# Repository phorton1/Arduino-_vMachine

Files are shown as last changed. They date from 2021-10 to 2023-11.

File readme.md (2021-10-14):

# The vMachine - Home

**Home** --
**[History](docs/history.md)** --
**[Hardware](docs/hardware.md)** --
**[Electronics](docs/electronics.md)** --
**[User Interface](docs/ui.md)** --
**[Software](docs/software.md)** --
**[Installation](docs/installation.md)**

The vMachine is a full featured proof-of-concept implementation of a **V plotter**.
It is essentially a CNC machine that uses *triangular kinematics* to work in a
cartesian coordinate system.

It is based on the inexpensive, yet powerful **ESP32** module, rather than the usual
Arduino class proessors.  The ESP32 can easily be programmed from within the
Arduino development environment and has *dual cores*, runs at *240 Mhz* (as opposed to
the Arduino at 16Mhz) and comes with *520KB* (as opposed to 2KB) *of RAM*.  In addition
the ESP32 includes full onboard **WiFi and Bluetooth** capabilities, and can be had for
$5, or about half the price of a genuine Arduino.

Therefore my *primary design decision* was to base this, and my future CNC projects
on an ESP32 processor.

**VIDEO - introduction to the vMachine**

The vMachine project is intended to accomplish several goals. Firstly, I wanted
to start developing and publishing open source CNC machines with the ESP32.
And so I built the machine and now present the designs and information
needed to build one.

The vMachine includes a full **Web Browser User Interface** so that it can be
controlled wirelessly from your phone or computer via **WiFi**.  It can also be controlled
via the **serial port** on the ESP32, via **Telnet** on port 23, or via **Bluetooth**
for usage with commonly available gcode sender programs.
Finally, it can also store gcode files on the optional **SD Card** and run jobs entirely
locally, right on the ESP32, via the optional **Touch Screen User Interface**, without
involving any other devices.

This repository includes all of the files and information needed to
build a copy of this machine.  It includes the needed to **3D print** the plastic
parts, as well as the underlying Fusion 360 designs if you need
or want to modify the 3D printed parts. It includes all of the **schematics**
and information needed to breadboard or otherwise create the electronic circuits,
as well as the KiCad files behind those, and the Flatcam and GCode files I used to
mill my own **circuit boards** for this version.

I have tried to provide a general roadmap for building a vMachine on these
pages.

A specific goal of this vMachine project is that it is generally scalable
to a larger machine, specifically one that can work with 4x8 feet sheets
of plywood, using a router to cut the plywood, as with the
[Maslow CNC](https://www.maslowcnc.com/).
Credits go to the Maslow team, as my vMachine source code actually
contains a port of the **Maslow triangular kinematics** to the ESP32.
I hope to build such a machine in the near future, and it should be
relatively straight-forward to scale this project up to a larger
machine of some sort.  The size of the machine is entirely parameterized
within the software and user interface.

But most importantly, this project establishes a **general approach** to
building ESP32 based CNC machines of various types, not only the vMachine
but also typical 3 and 4 axis CNC machines.  It is entirely based on the
next generation
[FluidNC](https://github.com/bdring/FluidNC)
project, a hugely important codebase that I have
forked and modified slightly so-as to better be able build projects
within the Arduino IDE development environment.

## Running the demo files

Included in this repository are a number of ready-to-go **gcode files**
that you can run on the vMachine.  It is beyond the scope of this project
to teach you how to use Inkscape, or Flatcam, or Fusion 360, or any other
available program to create gcode files to feed to the vMachine.

But, if you build the machine, and populate the SD card from this
repository, there are some gcode files you can use right away to
test it, verify it is working correctly, and even produce some nice
drawings.  You can view the contents of these gcode files to see what
kind of gcode the vMachine expects so that you can produce it with
any of the above programs, or by hand, as necessary.

**VIDEO - Running the Demo Files**

The video above demonstrates the touch screen UI, the browser
based Web/Wifi UI, and the serial terminal user interface by running the following
"programs" (gcode files) via one of the user interfaces:

- **homing** - first we "home" the machine
- **center.g** - moves the sled to the center of the page
- **ruler.g** - starts at the center and prints a simple ruler pattern
- **draw_boxes.g** - draws boxes on the board itself around the work area and 12x9" and 11x8.5" paper sizes
- **/test8.5x11/test8.5x11.ngc** - a sophisticated test that draws rulers, shapes, a compass and a sailboat
on 11x8.5" paper

When you get your vMachine working, the first thing you will print will probably be
the **ruler.g**, and you can do that by just manually moving the sled to the approximate
center of the work area, before you get **homing** working.   Once you can **home**
the machine, and you setup the G55 and G56 coordinate systems, you can run the
**draw_boxes.g** gcode to draw the work area, and 12x9 and 11x8.5 alignment boxes
directly on the board.  Then you can tape a piece of (US letter) paper in the
11x8.5 alignment box and print the **test8.5x11.ngc** reference test sheet on that.

## Documentation

The documentation starts with this page, and includes the following additional
pages:

- **[History](docs/history.md)** - my personal historical perspectives and
photos of early prototypes and previous versions of the vMachine.
- **[Hardware](docs/hardware.md)** - details the physical
construction of the vMachine, including the 3D printing and mechanical parts.
- **[Electronics](docs/electronics.md)** - the schematics and home made circuit
boards for the machine.
- **[User Interface](docs/ui.md)** - a synopsis of the behavior of the
vMachine and it's generalized **FluidNC_UI** user interface.
- **[Software](docs/software.md)** - an overview of the software architecture
of the vMachine and FluidNC.
- **[Installation](docs/Installation.md)** - instructions on building and installing
the vMachine firmware onto the ESP32 using the Arduino IDE environment.

It is recommended that you read all these pages BEFORE constructing a vMachine.
In my opinion if you are going to build a machine from these sources, or part of them,
you should **START** with the **[Installation](docs/Installation.md)**
page and the first thing you should do is *build the firmware and install it*
to a bare ESP32 dev module with just a USB cable.

As part of *that* process it is required that you verify and and utilize the browser
based WiFi UI to the module and upload some files to the file system on the ESP32,
so with just the bare ESP32 module you can verify that the firmware is installed,
test the Web UI, and make sure that it runs more or less correctly BEFORE investing
any time in 3D printing or creating breadboards or printed circuit boards.

In any case, all of these pages, and this source, is provided in the hopes that
you will find it useful and/or interesting.

## License

I'm gonna have to do something here.  Yech, I hate those headers in source files.

## Credits

- To the [Maslow CNC](https://www.maslowcnc.com/) team for the kinematics.

- To **bdring** and the [FluidNC Team](https://github.com/bdring/FluidNC) for the core of this project.

<br>
<hr>
<div style="text-align: right">
<a href='docs/history.md'>NEXT</a><i> - more about the vMachine ...</i>
</div>

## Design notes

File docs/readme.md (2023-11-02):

# The vMachine - Home

**Home** --
**[History](history.md)** --
**[Hardware](hardware.md)** --
**[Electronics](electronics.md)** --
**[Software](software.md)** --
**[Installation](installation.md)**

The vMachine is a full featured proof-of-concept implementation of a **V plotter**.
It is essentially a CNC machine that uses *triangular kinematics* to work in a
cartesian coordinate system.

It is based on the inexpensive, yet powerful **ESP32** module, rather than the usual
Arduino class processors.  The ESP32 can easily be programmed from within the
Arduino development environment and has *dual cores*, runs at *240 Mhz* (as opposed to
the Arduino at 16Mhz) and comes with *520KB* (as opposed to 2KB) *of RAM*.  In addition
the ESP32 includes full onboard **WiFi and Bluetooth** capabilities, and can be had for
$5, or about half the price of a genuine Arduino.

Therefore my *primary design decision* was to base this, and my future CNC projects,
on an ESP32 processor.

**TODO: VIDEO - introduction to the vMachine (good thumbnail for front image**

The vMachine project is intended to accomplish several goals. First, I wanted
to start developing and publishing open source CNC machines with the ESP32.
And so I built the machine and now present the designs and information
needed to build one.

The vMachine includes a full **Web Browser User Interface** so that it can be
controlled wirelessly from your phone or computer via **WiFi**.  It can also be controlled
via the **serial port** on the ESP32, via **Telnet** on port 23, or via **Bluetooth**
for usage with commonly available gcode sender programs.
Finally, it can also store gcode files on the optional **SD Card** and run jobs entirely
locally, right on the ESP32, via the optional
[**Touch Screen User Interface**](https://github.com/phorton1/Arduino-libraries-FluidNC_UI)
, without involving any other devices.

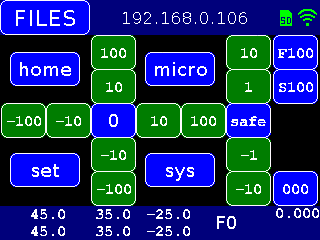
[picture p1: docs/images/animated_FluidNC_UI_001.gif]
(https://github.com/phorton1/Arduino-libraries-FluidNC_UI)


TODO: create animated gif specific to _vMachine

This repository includes all of the files and information needed to
build a copy of this machine.  It includes the files needed to **3D print** the plastic
parts, as well as the underlying Fusion 360 designs if you need
or want to modify the 3D printed parts. It includes all of the **schematics**
and information needed to breadboard or otherwise create the electronic circuits,
as well as the KiCad files behind those, and the Flatcam and GCode files I used to
mill my own **circuit boards** for this version.

I have tried to provide a general roadmap for building a vMachine on these
pages.

A specific goal of this vMachine project is that it is generally scalable
to a larger machine, specifically one that can work with 4x8 feet sheets
of plywood, using a router to cut the plywood, as with the
[Maslow CNC](https://www.maslowcnc.com/).
Credits go to the Maslow team, as this vMachine source code actually
contains a *port* of the **Maslow triangular kinematics** to the ESP32.
I hope to build such a machine in the near future, and it should be
relatively straight-forward to scale this project up to a larger
machine of some sort.  The size of the machine is entirely parameterized
within the software and user interface.

But most importantly, this project establishes a **general approach** to
building ESP32 based CNC machines of various types, not only the vMachine
but also typical 3 and 4 axis CNC machines or any other kind of machine
I might choose to build in the future.  It is entirely based on the
next generation
[FluidNC](https://github.com/bdring/FluidNC)
project, a hugely important codebase that I have
forked and modified slightly so-as to better be able build projects
within the Arduino IDE development environment.

<br>

## Running the demo files

Included in this repository are a number of ready-to-go **gcode files**
that you can run on the vMachine.  It is beyond the scope of this project
to teach you how to use Inkscape, or Flatcam, or Fusion 360, or any other
available program to create gcode files to feed to the vMachine. You
may use any of those, or any other program you wish, to create gcode
files for the vMachine.

But, if you build the machine, and populate the SD card from the **sdCard folder**
in this repository, there are some gcode files you can use right away to
test it, verify it is working correctly, and even produce some nice
drawings.  You can also view the contents of these gcode files to see what
kind of gcode the vMachine expects so that you can produce it with
any of the above programs, or by hand, as necessary.

**TODO: VIDEO - Running the vMachine Demo Files**

The video above demonstrates the touch screen UI, the browser
based Web/Wifi UI, and the serial terminal user interface by running the following
"programs" (gcode files) via one of the user interfaces:

- **homing** - first we "home" the machine
- **center.g** - moves the sled to the center of the page
- **ruler.g** - starts at the center and prints a simple ruler pattern
- **draw_boxes.g** - draws boxes on the board itself around the work area and 12x9" and 11x8.5" paper sizes
- **/test8.5x11/test8.5x11.ngc** - a sophisticated test that draws rulers, shapes, a compass and a sailboat
on 11x8.5" paper

When you build a vMachine, the first thing you will print will probably be
**ruler.g**, and you can do that by just manually moving the sled to the approximate
center of the work area, before you get **homing** working.   Once you can **home**
the machine, and you setup the G55 and G56 coordinate systems, you can run the
**draw_boxes.g** gcode to draw the work area, and 12x9 and 11x8.5 alignment boxes
directly on the board.  Then you can tape a piece of (US letter) paper in the
11x8.5 alignment box and print the full **test8.5x11.ngc** reference gcode on that.

TODO: Image of test gcode output

<br>

## Documentation

The documentation starts with this page, and includes the following additional
pages:

- **[History](history.md)** - my personal historical perspectives and
photos of early prototypes and previous versions of the vMachine.
- **[Hardware](hardware.md)** - details the physical
construction of the vMachine, including the 3D printing and mechanical parts.
- **[Electronics](electronics.md)** - the schematics and home made circuit
boards for the machine.
- **[Software](software.md)** - contains an overview of the
**software architecture** and details about how to **configure** the vMachine
- **[Installation](Installation.md)** - instructions on building and installing
the vMachine firmware onto the ESP32 using the Arduino IDE environment.

It is recommended that you read all these pages BEFORE constructing a vMachine.
If you are going to build a machine from these sources, or part of them,
you should **START** with the **[Installation](Installation.md)**
page and the first thing you should do is *build the firmware and install it*
to a bare ESP32 dev module with just a USB cable.

As part of *that* process it is required that you verify and utilize the browser
based WiFi UI to the module and upload some files to the file system on the ESP32,
so with just the bare ESP32 module you can verify that the firmware is installed,
test the Web UI, and make sure that it runs more or less correctly BEFORE investing
any time in 3D printing or creating breadboards or printed circuit boards.

In any case, all of these pages, and this source, is provided in the hopes that
you will find it useful and/or interesting.

<br>

## Please Also See

Please also see another CNC machine based on the same architecture,
my implementation of an ESP32 3 axis machine on an inexpensive
[**CNC 3018**](https://github.com/phorton1/Arduino-esp32_cnc3018)
from China [ebay](https://www.ebay.com/itm/392298131168).

These "machines"  are relatively small INO programs.  They are built on top of a
number of other libraries that provide the bulk of the functionality.

- [**FluidNC**](https://github.com/phorton1/Arduino-libraries-FluidNC) - the next generation **ESP32 GRBL** machine
- [**FluidNC_UI**](https://github.com/phorton1/Arduino-libraries-FluidNC_UI) - a *touch screen user interface* for FluidNC
- [**FluidNC_Extensions**](https://github.com/phorton1/Arduino-libraries-FluidNC_Extensions) - some extensions to FluidNC

The core of the machines, the GRBL (g-code) interpreter, is based on the
[**FluidNC**](https://github.com/phorton1/Arduino-libraries-FluidNC)
library.  The operational details of the machine, what g-codes
are supported, the basic serial command protocol, the wifi and webserver,
the machine configuration, and most functional aspects of the machine are
provided by this library.

On top of FluidNC I have built
[**FluidNC_UI**](https://github.com/phorton1/Arduino-libraries-FluidNC_UI),
the *touch screen user interface*, as a library that can optionally
used in ESP32 CNC projects.
Please see this library for a **description of the *User Interface***.

I have also added a
[**FluidNC_Extensions**](https://github.com/phorton1/Arduino-libraries-FluidNC_Extensions)
library that contains a number
of features that are used in this, and other machines based on this system.
This library contains methods and objects to abstract and extend the FluidNC
core.  Specific contents at this time include:

- some easy to use debug/info/error **output methods**
- methods to abstract the **state** of the FluidNC machine
- methods to abstract **control** of the FluidNC machine
- methods to supplement the FluidNC **configuration** system, and
- an implementation of **mesh bed levelling**

<br>

## Credits and License

This library is licensed under the
[GNU General Public License v3.0](https://github.com/phorton1/Arduino-_vMachine/tree/master/LICENSE.TXT)

**Credits**

- To the [Maslow CNC](https://www.maslowcnc.com/) team for the kinematics.
- To **bdring** and the **FluidNC Team**

<br>
<hr>
<div style="text-align: right">
<a href='history.md'>NEXT</a><i> - more about the vMachine ...</i>
</div>

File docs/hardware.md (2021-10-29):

# The vMachine - Hardware

**[Home](readme.md)** --
**[History](history.md)** --
**Hardware** --
**[Electronics](electronics.md)** --
**[Software](software.md)** --
**[Installation](installation.md)**

## Parts List

The following parts are needed and/or optional to construct the vMachine.

- the **board**
- two **NEMA 17 stepper motors**
- two one meter 4 wire **cables** with connectors for the stepper motors
- two 16 tooth 5mm GT2 **pullies** for the stepper motors
- two meters of 5mm GT2 **belt**
- one MG90 **RC Servo**
- one meter 3 wire **cable** with connectors for the servo
- two **infrared sensor boards** (from the [Electronics](electronics.md) page)
- two one meter 3 wire **cables** with connectors for the infrared sensors
- one **vMachine control board** (from the [Electronics](electronics.md) page)
- (optional but highly recommended) *SD Card Module*  for the vMachine board
- (optional) three *WS2812b LEDs* cut from a led strip with 3 wire cable and connector soldered on
- (optional) 3.2" 320x240 SPI TFT *Touch Screen* with the **lcd connector and cable** from the [Electronics](electronics.md) page
- two dabs of white acrylic paint, or two small pieces of white electrical or aluminum duct tape
- a variety of **lead fishing weights**

as well as the **3D printed parts** shown on this page, along with a variety
of M2 and M3 (2 and 3 mm) **machine and wood/metal screws**.

## 1. The Board

The board is 28.75" wide by 24" high from 1/2" or 3/8" plywood.

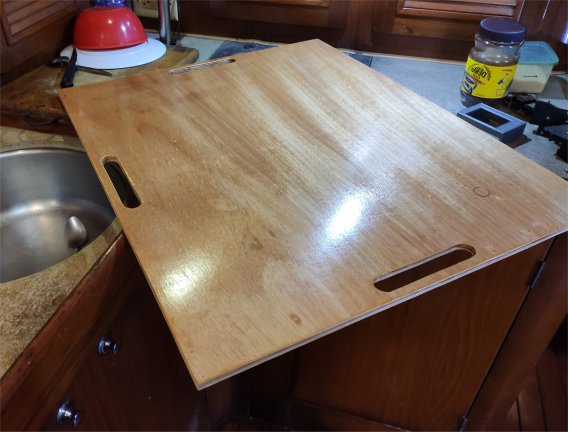
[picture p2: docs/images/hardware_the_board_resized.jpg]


I cut some hand-holds into mine and finished it with clear polyurethane.

I drilled the holes for the screws and wires after preparing the board.

<br>

## 2. Motor Mount and Infrared Sensor Assembly

I generally print everything from PLA with 0.3mm layer heights in draft quality for speed,
unless otherwise noted.  The first files printed from the **stl directory** are the
**motor_mount_left** and **motor_mount_right**.

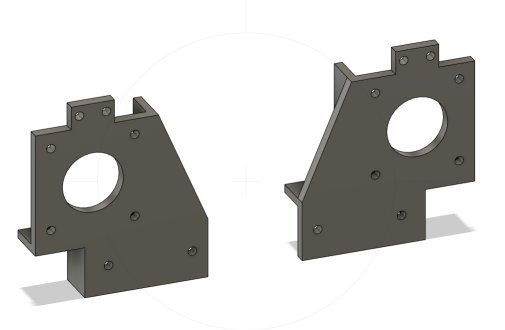
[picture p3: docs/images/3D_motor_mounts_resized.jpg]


I print these "face down" with no supports.

Then *two sets* of the **sensor_housing** and **sensor_top** are printed in the orientation
shown below so they also need no supports.  Because they are small and detailed, I printed
these at 0.2mm layer heights in "quality" smode.

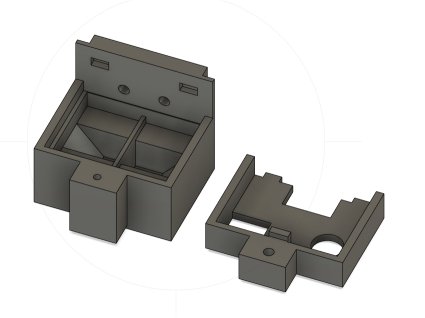
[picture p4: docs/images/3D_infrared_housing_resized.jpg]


Assembly then proceeds as follows.

The pulley is attached to the Nema17 motor with two included set screws and the motor is
attached to the motor mount with four M3x6 machine screws.  The combination is then attached
to the wooden board with two M3x12 self threading (wood/metal) screws into small (1/16") holes
drilled into the board using the motor mount as a template.

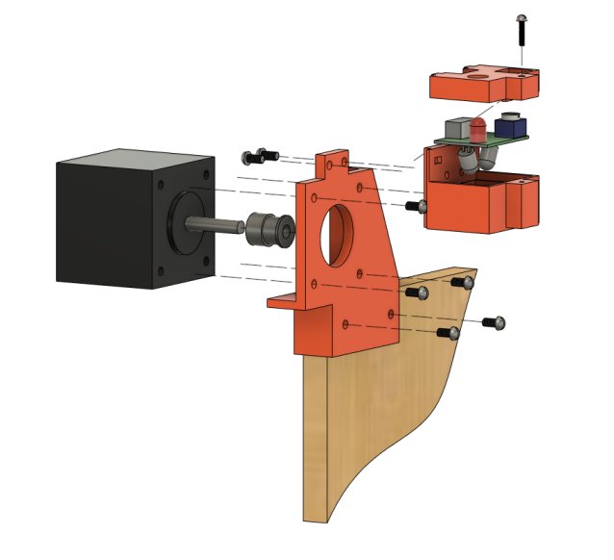
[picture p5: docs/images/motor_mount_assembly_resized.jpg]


The infrared sensor housing is attached to the motor mount from the rear by two M3x6 machine
screws directly into the plastic, then the
sensor circuit board is placed inside and the sensor body top is snapped into place and/or
secured with an M2x10 machine screw from the top directly into the plastic.

The process is repeated for the other side of the board.

<br>

## 3. 3D Print Sled Parts

The sled consists of several parts

- the **sled_base**
- the **sled cap**
- the **left and right bearings**
- the **pen_shaft** and **pen_tip**
- and the **servo arm**

The sled parts are all printed without supports.

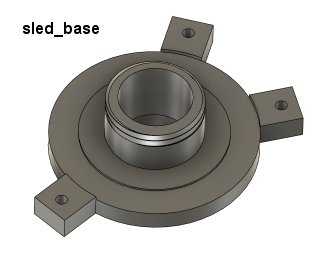
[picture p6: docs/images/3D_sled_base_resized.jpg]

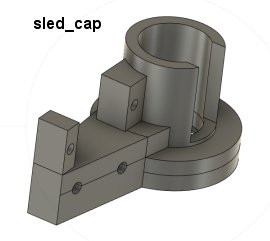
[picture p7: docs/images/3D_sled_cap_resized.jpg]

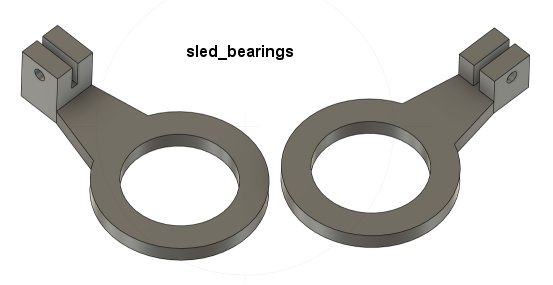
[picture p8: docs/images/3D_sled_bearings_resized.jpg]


The **sled_cap** screws onto the sled_base, allowing a little room for the sled bearings to
turn while still snugly holding the RC Servo in a more-or-less vertical orientation.

Note that the left **sled_bearing** is taller than the right **sled_bearing** and goes on the bottom.
I sanded the bearing faces to make them as smooth as possible.  Later we will put a little
grease or other lubricant on them as it is important that they rotate about the sled_base
as freely as possible once the sled cap is screwed on.

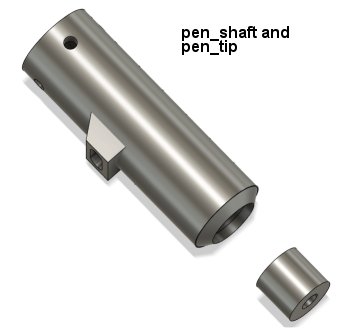
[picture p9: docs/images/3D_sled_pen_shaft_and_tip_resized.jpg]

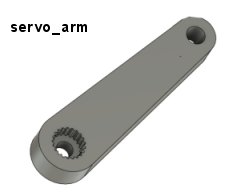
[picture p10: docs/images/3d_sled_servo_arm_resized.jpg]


The **pen_shaft** is printed vertically with the *top down* (upside down).  I printed the
pen_shaft, pen_tip, and servo arm with 0.20mm layer heights in a quality setting on my Prusa.
Before assembling I also put the pen shaft in a drill and turned it while sanding as best I
could to make it as smooth as possible. I also sanded the inside of the pen cap a bit.
It is important that the pen_shaft move freely in the pen-cap.

The **pen_tip** is printed without supports, but with a **4 or 5mm "brim"** for stability.
It is printed vertically with the *top up*.  The shaft and tip are designed to accommodate a
**0.5mm Sharpie** felt pen.  While testing, the **pen_tip** part can be moved
up and down inside the pen shaft until you get it so that the tip of the felt pen just barely
touches the board (and lifts the whole assembly up off of the board about 1/2mm) when the
servo arm is "down".

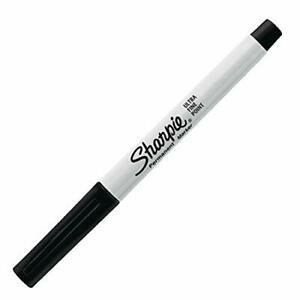
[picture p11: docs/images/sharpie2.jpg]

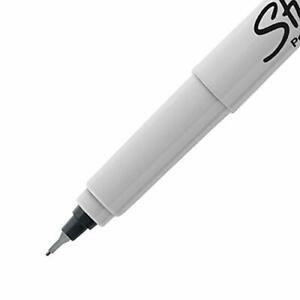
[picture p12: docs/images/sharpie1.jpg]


The pen shaft is designed so that when the **servo_arm** is down, it automatically centers itself
in the pen base (due to the beveled angles).  The adjustable pen_tip allows you to adjust the actual
contact of the pen with the paper while the shaft is fully down.  The tip of the Sharpie felt pen
should extend past the base about 1/2 mm when the servo arm is completely down, and it should not move around from
that position.

<br>

## 4. Sled Assembly

The parts for the sled should be printed and dry-fitted to make sure the bearings move smoothly
around the base and that the pen_shaft travels smoothly up and down in the sled when assembled.

The pen_shaft was designed with tight tolerances, with the specific idea that the shaft
and inside of the sled_cap would be sanded smooth after printing, so they may not slide
freely immediately after printing.  It is difficult to sand the inside of the sled_cap/base,
and care should be taken when sanding the pen_shaft itself so as not to introduce wobble
or too much looseness.  One way or the other it is key that the pen shaft move smoothly
up and down and that the bearings are free to rotate.  So you must sand things and/or
even re-slice and reprint them as necessary until you get a good working set of sled parts.

A dry or wet lubricant may be helpful.  I used a little silicon grease but I think it
is a bit heavy.  Some light lubricating oil or a dry graphite lubricant might
work better.

Once the sled parts have been printed and dry fitted and you are satisfied with them,
assembly of the sled may proceed.

### 4a. Attach Belts to the Bearings

Attach one meter of GT2 5mm belt to each of the two bearings as shown
with one M3x6 machine screw threaded into the plastic.

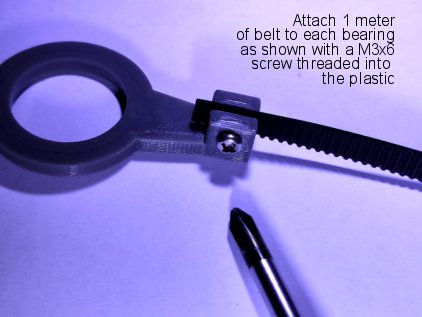
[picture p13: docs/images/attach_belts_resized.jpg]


### 4b. Measure and Place the Zero Marks on the Belts

I initially started by *painting* a white stripe on the black GT2 belt with
acrylic paint.  That worked ok, but it turned out to be easier to just cut
a small piece of white electrical tape and stick it on the belt.  Then, in
the end, I found that I got a better "signal" for the infrared sensors if,
instead of white paint or tape, I put a small piece of **reflective aluminum
tape** on the belt.

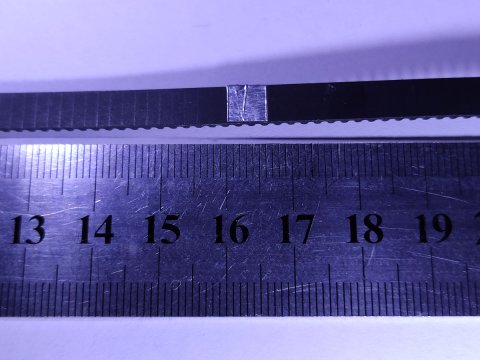
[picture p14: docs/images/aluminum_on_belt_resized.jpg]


The aluminum duct tape is fairly available and inexpensive and comes in
2" wide rolls and is useful for other things, and we only need two small
5x5mm squares of it, so I recommend using it if you have it, but white
paint, fingernail polish, or white electrical tape can be substituted as
needed.

In any case, we need to make a 5mm wide stripe of some kind on the belt
starting at 200mm from the center of the sled.  So we will paint the area
on the belt that will be from 200mm to 205mm from the center of the sled.

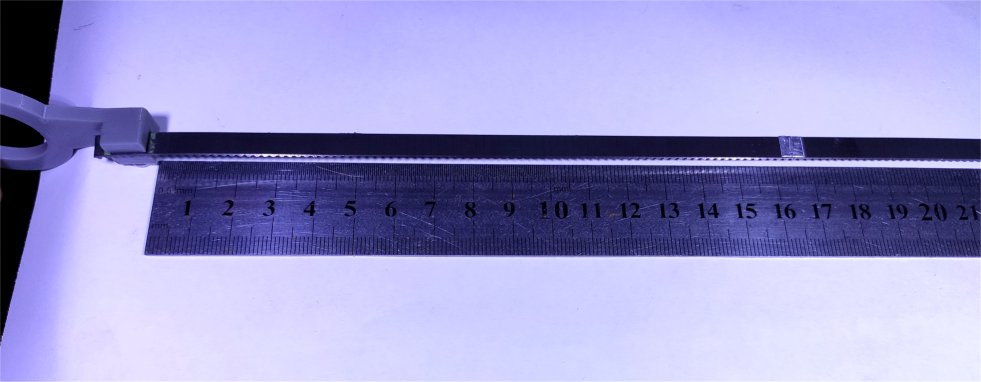
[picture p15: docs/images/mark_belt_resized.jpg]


The *edge of the belt attachment is exactly 40 mm* from the center of the sled.
So we need to make the zero marks an additional **160mm** along the belt from there,
so that it will end up at 200mm from the center of the sled.

Place a ruler against the edge of the belt attachment and measure **160 mm** along
the belt. That will be the "leading edge" of the zero mark.  Place the aluminum
or electrical tape, or paint the line, starting there and proceeding away from
the sled for 5 mm.

Another reason I prefer the tape approach to the paint approach is that you
can replace it or move it as necessary.  The paint tends to peel off in time,
as does the tape, so they will likely need to be refreshed over the lifetime
of the machine.  The tape is easier to use and easier to replace.

### 4c. Assemble the Sled Base

Place the left bearing on the sled_base, then place the right bearing on
top of it, and screw the sled_cap on snugly (but not overly tight).  It
should be the case that the bearings still turn freely when the cap is snug.

It should also be the case that when the cap is snug and the bearings are
in their proper positions that the servo will be oriented downward, along
with the two weight attachment points, and the single centered weight attachment
point will be pointed upwards.

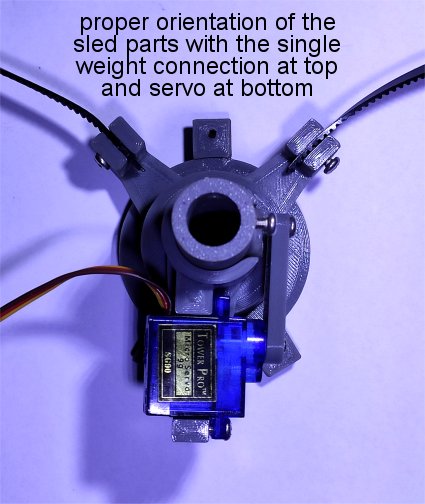
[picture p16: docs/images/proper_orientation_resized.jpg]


### 4d. Attach and Test the Servo

The servo is a tight fit.  Cram it in there.  It barely needs a screw,
but I used one M3x6 screw, threaded directly into the plastic of the
sled_cap to secure it.

(This section assumes that you have already installed the needed software,
and built and uploaded the firmware to the ESP32.  Please see the
**[Installation](installation.md)**
page for more details.

Before attaching the stepper motors or high-voltage (19.5V) power supply,
we want to run the ESP32 on USB power and verify the functionality and
positioning of the RC Servo.

Attach the servo to the circuit board with its cable and boot the ESP32
up with a serial monitor connection by plugging the USB cable into your
computer.  You can use the Serial Monitor in the Arduino IDE to access
the ESP32 firmware.

In the default machine coordinate system, the servo moves between 0 and -90
(minus ninety) degrees (clockwise from the top of the servo), where -90 degrees
(clockwise) is in contact with the paper.
At that  point the servo arm will be slighly below parallel to the paper,
and the pen_shaft will be more or less "locked" in a full down position.
We call this the **pen down** position.

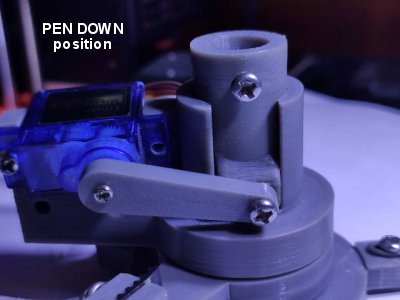
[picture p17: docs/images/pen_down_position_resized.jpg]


If we back the servo off about 20 degrees, to -70 degrees (minus seventy)
it will turn counter clockwise and lift the pen off the paper cleanly.
We call this the **pen up** position.

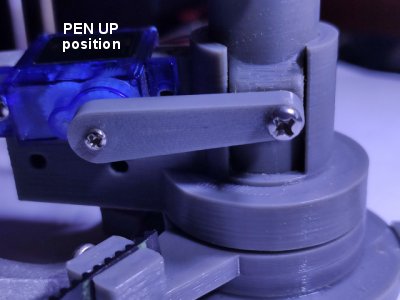
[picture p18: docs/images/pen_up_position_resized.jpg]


However, until we hook the servo up to the circuit board the first time, there
is no way to tell what position the servo is in. So, before even attaching the servo
arm, make sure the servo moves as expected by entering the following GCODE commands
into the monitor terminal.

```
G0 Z-90
```

is the command to send the servo to the "pen down" position and

```
G0 Z-70
```

is the command to send the servo to the "pen up" position.  As you type these
into the serial monitor and press the **Send** button
the servo should move and the firmware should respond
each time with "ok" as in the below photo of the Arduino Srial Monitor.

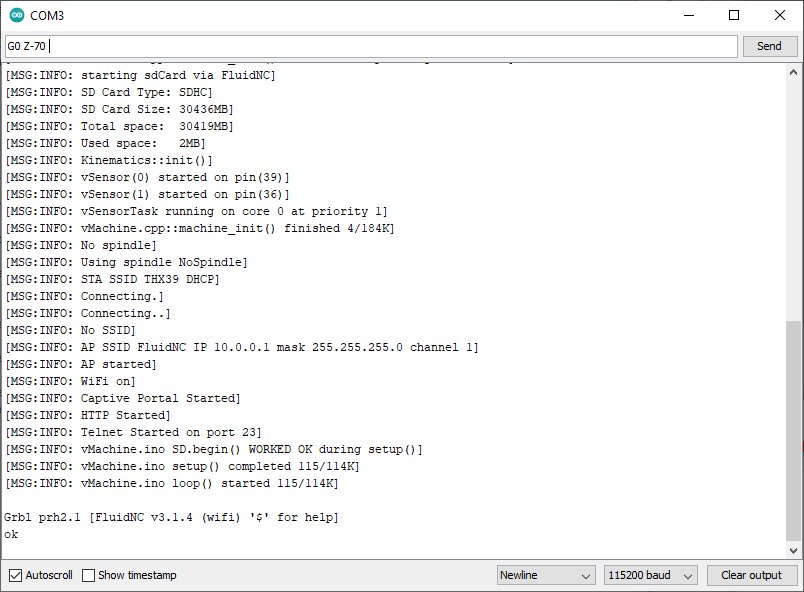
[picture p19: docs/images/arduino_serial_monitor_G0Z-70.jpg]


By entering these commands alternatively, one after the other, you should see the servo move
predictably clockwise or counterclockwise 20 degrees.  You can try other values
too.  In general just *play* with the servo using the serial monitor until you
are confident you can control it.

Once you can control it, you can go to the "pen up" position with "G0 Z-70"
and attach the servo arm with it's screws.  The servo arm should be just slightly above
parallel to the sled_base bottom at that point as in the below photo:

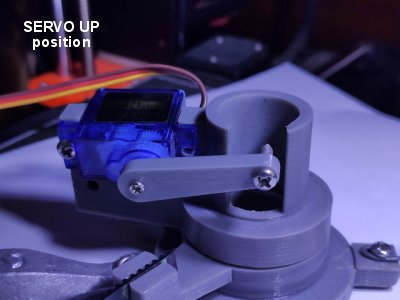
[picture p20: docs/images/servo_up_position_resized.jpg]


Then the "pen down" command (G0 Z-90) can be issued and the servo arm should
move to the following approximate position:

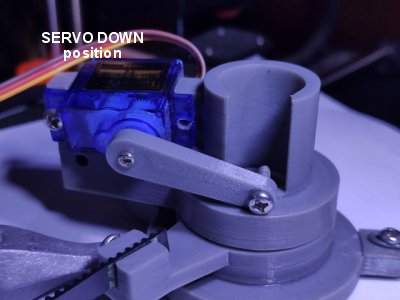
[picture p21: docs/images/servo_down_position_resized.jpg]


**REPEAT and TEST** the servo position until you are satisfied.  You can then
turn the machine off (unplug the USB cable) and the servo will move freely.
Turn the servo arm counter-clockwise till it points straight up, and **insert
the pen_shaft** into the assembly **while turning the servo arm clockwise**,
engaging it with the servo arm as you go.
You should find that you can easily remove and insert the pen_shaft by
manually moving the servo arm at the same time you turn the pen_shaft
as you insert or remove it.

When sent to the "pen down" position the servo should snap the pen_shaft to the down position
and lock it in place, but not have so much force that it is stressing the servo or plastic.
If turns too much, or too little, remove the servo arm and turn it one notch in the needed
direction, and re-attach it, and re-test.

Continue playing with these GCODE commands and the servo motor on your desk
until the servo reliably moves between the pen-up and pen-down positions
with the minus-70 and minus-90 gcode commands.

### 4e. Insert the **pen_tip** part and a Sharpie for calibration

It's easier to play with this part on your desk than on the machine, so
let's setup the Sharpie pen position before mounting more stuff.

The **pen_tip** part is inserted into the end of the pen_shaft.  You should find
that it is a snug fit as-is from the 3D printing.
With the **pen_tip** part inserted into the **pen_shaft** you
should be able to insert a **Sharpie** into the assembly such that the tip of the
Sharpie just protrudes past the end of the pen_shaft by a mm or two as in
the below photo.

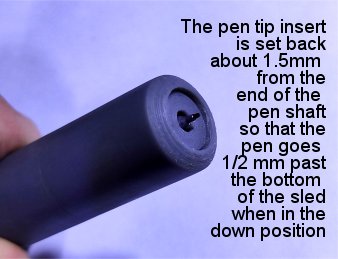
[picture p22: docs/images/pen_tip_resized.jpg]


You can adjust the position of the **pen_tip** part by moving it in or
out of the **pen_shaft** as needed.   When everything is correctly positioned
and the pen_shaft is inserted in the ***sled_base***, and the servo is in the
"pen down" position, the tip of the Sharpie should protrude just past the
bottom of the sled_base by approximately 1/2 mm.

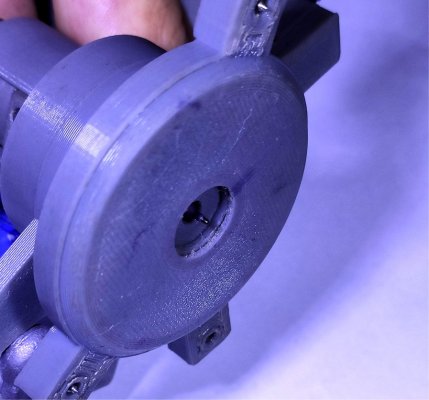
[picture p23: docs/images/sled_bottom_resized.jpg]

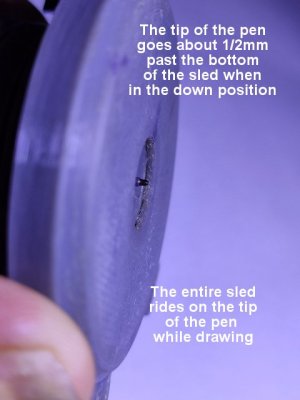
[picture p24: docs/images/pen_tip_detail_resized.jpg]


**DONT GLUE IT YET!!**   Later when the entire machine is working,
you can remove the Sharpie and the pen_shaft add a tiny drop of super glue to the
pen_tip part to secure it within the pen_shaft.   For now however, remove the
Sharpie and proceed to the next step (attaching the weights).

<br>

## 5. Attach the Weights

OK, I have put off talking about the lead weights as long as possible.

Your mileage may vary, and some experimentation may (will) be necessary.

On my machine I have the following lead fishing weights attached:

- 5 ounces (a little over 1/4 lb, or about 140 grams) at the end of each belt
- 1 ounce on a piece of wire off the top of the sled
- 2 ounces on the right lower side of the sled.



Attach the belt weights however you like.  I threaded the belt through
a ring on the 3 oz weight and through a washer so that it is adjustable.
Then I hung the two one ounce weights on a piece of wire from that.

The lead weights serve two main purposes.   First of all the weight of the
sled and the weights at the ends of the belt keep the belt engaged with
the motor pullies.  Without any weights the belt would slip and be useless.

In addition, the weights on the sled were carefully chosen, and placed, through
much experimentation, such that when the pen is "down" the ENTIRE SLED IS LIFTED
OFF OF THE BOARD and the only part of the sled contacting the board (the paper)
is the tip of the pen.




The weights on the sled are attached with M3x5 wood/metal screws.  **It is important
that the heads of the screws do not protrude past the bottoms of the holes!!**.
The right-bottom weight is attached directly with a screw.  The top weight
is fitted on a piece of steel wire with a loop bent in it for the screw.

It's a balancing act.  We are also trying to keep the rotational orientation of the sled
more or less fixed, so the heavier weight at the bottom serves that purpose: to
keep the servo pointed downwards.

A slight weight is needed above the sled to allow it to balance on
the pen tip.  When weighted correctly, in a perfect world, when
in the "pen down" position, the sled will balance entirely on the tip of the
felt pen and no other part of the sled will in contact with the board or paper.

*(Note that the board itself leans against a wall at a 8-12 degree angle from vertical.
The amount of force and balance on the pen-tip can also be varied by adjusting the
board's tilt angle).*

Here is a photo of the **fully assembled sled**:



It doesn't have to be exact, but the closer you can get to having the
sled balance on the tip of the pen when in the "pen down" position, the
better the accuracy of the machine will be.

Otherwise the machine will "ride" on an edge of the sled
as the belts pull it around and it could have a tendency to tilt
and turn as it moves.  But if balanced properly, only the tip of the pen will touch,
and since the pen tip is at the center of the sled, then the forces from the belt will always move
it, more or less exactly as expected.

<br>

## 6. Mount the Circuit Board and Run Cables

I made some "extension cables" for the sensors,
drilled a 3/4" hole for the cables in the bottom right corner of the
board, and taped the cables to the back of the board.




Then using four M3x12 wood/metal screws and four plastic spacers,
I mounted the circuit board to the wooden board.




The board must be mounted **well out of the way of the sled and cables** in
any position the machine might find itself in, so I chose the bottom right
corner of the wooden board.   The circuit board is mounted just below, and
to the right, of the hole that I drilled for the cables to come through.

<br>

## 7. Mount the Optional Touch Screen and/or LEDs

Mount the Touch Screen in the LCD housing with four M3x8 screws and
bolts.  Tighten the screws snugly, but not so tight as to warp the
plastic or Touch Screen.




Press the WS2812B LCD strip into place and secure it with the
LED cover piece and two M2x5mm screws directly into the plastic.




You can then mount the entire assembly just above the circuit board and
attach the LCD connector and LED strip connectors to the circuit
board.

<br>

## 8. Hang the sled and belts on the machine

The entire tangle of belts, weights, and the sled now form a sub-assembly
that can be placed, or removed, in total, from the vMachine by just hanging
it from the two motor pullies.



You probably want to remove the sled sub-assembly, all the belts and weights
off to the side while you finish the board and mount the Circuit Board to it.

<br>

## 9. Sensor Test and Adjustment

Another thing we can do before we attach the high-voltage power supply
is to calibrate and test the infrared zero sensors.

This is done by moving the belts back and forth and adjusting
the screws on the trim potentiometer on the Sensor circuit board
so that the LED turns **ON** when the aluminum strip passes under
the sensor, but turns **OFF** when the strip is not under the
sensor.

<br>

## 10. Plug in the Stepper motors and high-voltage power supply

Finally we plug the thing in and turn it on and verify the stepper motors work.

If the stepper motors and the sensors are working, we should be able to do a
"Homing" cycle and execute the "center.g" test gcode.

If the pen Z position in the sled is properly calibrated and the servo is working
properly we should be able tape a piece of paper to the board based approximately in the center,
and to run the "ruler.g" test gcode and do our first print!

If that is working well (and we have setup the G55 and G56 coordinate systems
as per the [Installation](installation.md) page), at some point we *may* want to run the "draw_boxes.g"
gcode file which will draw some boxes directly on "the board" that will then allow
us to align 11x8.5 or 12x9 pieces of paper to be taped to the board for more printing.

The project is considered completed when one can print the
the 11x8.5 or 12x9 test sheets and they come out nice.

<br>

## 11. Finished!

And at that point, the vMachine is essentially complete!

TODO: Image of finished vMachine

<br>
<hr>
<div style="text-align: right">
<a href='electronics.md'>NEXT</a><i> - Electronics and Circuits ...</i>
</div>

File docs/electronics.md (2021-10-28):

# The vMachine - Electronics

**[Home](readme.md)** --
**[History](history.md)** --
**[Hardware](hardware.md)** --
**Electronics** --
**[Software](software.md)** --
**[Installation](installation.md)**

This page has the schematic for the main vMachine **controller board**, as well
as the infrared **sensor board** and a small pcb used as the **lcd connector**.

The **controller board** has a number of features on it that you may or may not
want and that may be considered "optional" in the bigger scheme of things.



- eight pin display connector
- three pin ws2812b led strip connector
- power supply jack and step down buck convertor

even the SD card could be considered optional:

- six pin SD Card module connector

It is also possible, with a little effort, to create your own
circuit either on a breadboard, or a PCB and still take advantage
of this software using these schematics as guidelines rather than
verbatim.  In general the ESP32 pin assignments are somewhat flexible
and can be modified in the firmware and build process.

You may want to breadboard a vMachine incrementally, using a bench or
other power supply for the steppers and NOT getting 5V for the
ESP32 via buck down from the high power supply.  You may want
to utilize a different kind of sensor, or do something else with
the code and pins.

However, for the so inclined, included is the schematic, the kiCad
files behind the schematic as well as the flatcam and gcode files
needed to mill the PCB.  It would be a simple matter to produce a
pcb printed in China from a real board supply company, however, all
of my projects are essentially one-offs, so I am using the home-made
PCB approach.

## The Controller PCB

The controller board has the following connectors:

- a 38 pin slot for the **ESP32 Dev module**
- two 16 pin slots for **a498 Stepper Driver modules**
- a 6 pin connector for the **SDCard module**
- two 4 pin connectors for the **Stepper Motors**
- two 3 pin connectors for the **Infrared Sensors**
- a 3 pin connector for the **RC Servo**
- an 8 pin connector for the **TFT Touchscreen**
- a 3 pin connector for the ws2812b **LED Strip**
- a high power (12-24V) input jack
- a 2 pin **jumper for the 5V** from the buck step down convertor to the Esp32

Here is the schematic

vMachine_controller_schematic.pdf

You can ignore all the boxes labelled "v00" through "v100".
I did not know how to "untent vias" in kiCad when I made this and so
I put all my vias in the schematic as single pin connectors.

The kiCad footprints and milled circuit board make use of my own "footprints" so that
I could get a simple consistent large pad size for my initial attempts at learning
to mill PCB boards.



By far the hardest part of the production process was milling the green UV solder
resist epoxy off of the pads where I needed to solder.  Below is a picture of the circuit
board, still on the cnc machine, after removing the solder resist.

TODO: add hackaday blog/page(s) for
my spring loaded collet design and
my experiments with laser curing of UV photoresist and
link to them from here



**CAUTION:** after soldering the headers, connectors, and components
to this board
**BEFORE** inserting the ESP32 MODULE or connecting any other connectors,
please verify the circuit with a multi-meter for shorts and connections,
and then *PLUG IN THE POWER SUPPLY, TURN IT ON, and *ADJUST THE BUCK
CONVERTOR* TO PROVIDE 5V for the ESP32 5V PIN*.
Only after you have done the buck convertor voltage calibration
is it safe to plug in an ESP32 module and/or put the jumper on
the board which sends the 5V to the VIN pin of the ESP32.

These particular buck convertors come from the factory at
a "50% setting" meaning they will burn your ESP32 out if
you use a 20-24V power supply, by sending 10 or 12V to the
ESP32 which is only rated at 5V!!!




<br>

## The Infrared Sensor Board

This board runs on 3.3V and uses a pair of IR leds, one as an emitter and one
as a detector. The clear LED is the emitter.  I found that the black one worked well as
a detector. Both are generic 940nm leds that I bought in bulk (like 40 for $10)
some time ago.   The circuit uses uses a LM393 opamp as a comparator and
a variable 10K resistor to set the voltage level (light level) which will
trigger the sensor and there's a red LED on the top that lights up when the
sensor is triggered.



I believe this circuit is substantially the same as the robotic "infrared
obstacle avoidance modules" that sell on ebay for $1.50 or less like
the one below:



One can probably substitute that module verbatim, and some different 3D printing,
within this project to effect the same sensor without having to build a circuit board
and without changing any other software or circuits.  But I had the LEDs and I wanted
the orientation of them in a particular way over the belt and in a square, not a long
rectangular off centered box, over the stepper motors. Plus I'm having fun milling
PCB boards :-)

So I learned to use the LM393 (my first op-amp circuit) and designed and
implemented this board for the vMachine.



The milled PCB's came out pretty nice and it was easy to solder the parts to them:




They fit nicely into the 3D printed housings over the stepper motors,
and when adjusted they reliably detect the aluminum tape strip on the
vMachine belts.




Two of these boards are needed for the vMachine project.

<br>

## LCD Connector (board)

The **LCD Connector** cuts the number of pins from these generic SPI TFT touch
modules from 15 down to 8.   A number of the lines are duplicated for the
touch portion of the module (MOSI, MISO, and SCK) and others are merely held
high via resistors from the 5V VCC line.




The images below are of a previous (but exactly the same electronically) version
of the PCB that was larger and had mounting holes.  There are no mounting holes
for the LCD connector anymore.  It fits snugly enough without being screwed on.



After populating the board, I just re-arrange the pins slightly and
solder a pre-wired JST 8 pin header to the board and, after testing,
slap some hot glue on the wires  for stress release.  The other end
of the wires has a female 8 pin JST connector that plugs into the 8 pin
connector on the controller board.



<br>
<hr>
<div style="text-align: right">
<a href='software.md'>NEXT</a><i> - Software Architecture and Configuration ...</i>
</div>

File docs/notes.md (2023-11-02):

This notes.md contains various notes to myself.

## Realtime Architecture

```
    void IRAM_ATTR Stepping::onStepperDriverTimer() {   // always init'd not always started
        ++isr_count;
        timerWrite(stepTimer, 0ULL);
        timerAlarmEnable(stepTimer);
        Stepper::pulse_func();
    }

    void Stepping::init() {
        log_info("Stepping:" << stepTypes\[_engine].name << " Pulse:" << _pulseUsecs << "us Dsbl Delay:" << _disableDelayUsecs
                             << "us Dir Delay:" << _directionDelayUsecs << "us Idle Delay:" << _idleMsecs << "ms");

        // Prepare stepping interrupt callbacks.  The one that is actually
        // used is determined by startTimer() and stopTimer()

        const bool isEdge  = false;
        const bool countUp = true;

        // Setup a timer for direct stepping
        stepTimer = timerBegin(stepTimerNumber, fTimers / fStepperTimer, countUp);
        timerAttachInterrupt(stepTimer, onStepperDriverTimer, isEdge);
        ...

    void Stepping::startTimer() {
        if (_engine == I2S_STREAM) {
            i2s_out_set_stepping();
        } else {
            timerWrite(stepTimer, 0ULL);
            timerAlarmEnable(stepTimer);
        }
    }
    void IRAM_ATTR Stepping::stopTimer() {
        if (_engine == I2S_STREAM) {
            i2s_out_set_passthrough();
        } else if (stepTimer) {
            timerAlarmDisable(stepTimer);
        }
    }
```

## Ideas for SDCard rewrite

1. Implement the SD State as a bitwise value
2. Initialize the SD Card, if present, at startup with notification.
3. Implement a low priority task to check for SD Card insertion and removal
4. Issue CLIENT_ALL notifications upon idle removal and insertion of SD Card
5. Issue CLIENT_ALL Alarms upon ANY SDCard error, including detecting removal
   while a file/dir is open.
5. DONT start() and end() the SD card willy-nilly all over the place
6. Allow concurrent access where it makes sense.
7. Really should STOP using the state of the SDCard as a behavior semaphore.
   The concept is really a "job is running" which *should* be doable from
   a client (I want exclusive access to the gcode machine) (i.e. by % sign)
   as well as from the SD Card.

   HOWEVER that is beyond my scope for today, so the notion that an
   SDCard job is running will continue to preclude other GCode from
   running, but otherwise, it's first-come first served.

THE BIGGEST SCARY ISSUE is that, at a low level, accessing the SDCard
or SPIFFs will upset the motor control or other intrrupts. I think it
is true for SPIFFS (the "EEPROM") from my readings. HOWEVER I don't see any
code that indicates that anyone tried to prevent that particular issue.
It seems to be more about protecting the GCODE machine from getting mixed
up WHILE a job was running than protecting the GCode machine from timing
interrupts due to the job running.

All I can tell you is that it was a mess, using the SDState as a semaphore
for all kinds of behaviors.

## G codes, M codes, SD Card, Jobs, and multiple concurrent interfaces

Yikes. Yech.

There is no standard for G codes and M codes.  There are only implementations.

There are purported standards (i.e. GRBL 1.1) but they are not technical specifications.

The field is vast, wide, and wild.

### Lack of "job" demarcations

In 'gcode' there is no standardized encapsulation of a "job".

Note that there is not even a documented "standard set" of gcodes
related to GRBL 1.1 .. try to find it!  If you dig, you will get
a disclaimer that GRBL is a "beta" thing, and a "discussion" of
the gcodes is available at https://wiki.shapeoko.com/index.php/G-Code

From that page: "Program Start/End --- this is traditionally indicated by a "%" symbol
--- since most controllers ignore anything else on the line it may
be abused as a way to insert a comment."

Handy.

There is no consistent concept for starting and ending jobs
with streaming interfaces, except, perhaps in the G28? "send
file to the SD card" command, where the percent signs (should
be) (are) mandatory to signal the start end end of the file
for transmission over the serial port.

### Gcode Analsyis

For completeness, please note the following RepRap M codes which are
NOT part of GRBL ... these codes have completely different semantics
in GRBL and there are no equivilants in FluidNC:
```
    M21 Initialise (mount) SD Card
    M22 Release (unmount) SD Card
    M23 Select File for Printing
    M24 Start / Resume SD Card Print (see M23)
    M25 Pause SD Card Print (see M24)
    M26 Set SD Position in bytes
    M27 SD Print status
    M28 Write programm to SD Card
    M29 Stop writing programm to SD Card
```

## Relative Coordinate Systems

When you press the "zero xyz" button in the WebUI it emits this command:

G10 L20 P0 X0 Y0 Z0

This tells the machine to assign the coordinate system 0 (P0)
zero relative to the current positions (L20) of the machine XYZ ... Here
we did that when the machine was at 200,150,4.

(G10 L2 lets you set the numbers directly)

If you type $# you can see the machine's coordinate systems:
```
    $#
    [G54:200.000,150.000,4.000]
    [G55:0.000,0.000,0.000]
    [G56:0.000,0.000,0.000]
    [G57:0.000,0.000,0.000]
    [G58:0.000,0.000,0.000]
    [G59:0.000,0.000,0.000]
    [G28:0.000,0.000,0.000]
    [G30:0.000,0.000,0.000]
    [G92:0.000,0.000,0.000]
    [TLO:0.000]
    [PRB:0.000,0.000,0.000:0]
```

G54 through G59 define six coordinate systems that you may
change between  G28 and G30 are predefined positions, and
G92 is a coordinate system offest.

They can be cleared with $RST=#

Note that one of these is always active.
And that G54 really serves as the "default" machine setup.
It should really NOT be used by the WebUI IMHO ...

The following command sets 0,0 to the bottom left
corner of a 12x9 paper centered in the work area
at z=4.

    ; 12 * 25.4 = 304.8
    ; 9 * 25.4 = 228.6
    ; (400-304.8)/2 = 47.6
    ; (300-228.6)/2 = 35.7

    G10 L2 P2 X47.6 Y35.7 Z4    ; define the P2=G55 coordinate system
    G55                         ; switch to it

By not using G54, which we save as the default coordinate system,
we can return to 'machine' coordintes by merely executing G54

    G54

I can now adjust the Z height with
    G10 L2 P2 Z3.4

And just have inkscape "GOTO ZERO" for the Z-Axis, whatever
that is.

And can either switch to the G55 coordinate system manually,
or via the header/footer in inkscape

## COORDINATE SYSTEMS DETAILS

motor_steps = an array of int32s representing the stepper motor position in steps
motor position = floats in mm's == sys_position / axis_settings->steps_per_mm
machine position = floats called "mpos" which is the cartesian coordinate within the work area,
work position =  floats (wpos) that lets you set 0,0 relative to the machine area.

The "motor position" and motor_steps are representative of the chain (cable) lengths.

The system does not maintain the motor, machine, or work positions.
It only maintains the int32 sys_positions.

If FluidNC needs to do something in the machine/work coordinate systems (i.e. move to the
next point in some gcode) it calls cartesianToMotors() to get the "motor positions"
for that coordinate, which it then turns back into sys_position steps for planning
and actual movement.

For reporting, motor_steps is turned into the "machine position" by
calling motors_to_cartesian() (forward kinematics), which in turn, does
iterative calls to the reverse kinematics to find a "machine_position" that matches
the motor position.  These forward kinematics are normally not needed to run FluidNC,
they are used only for reporting.

## HOMING AND ZERO STOPS

OLD NUMBERS!

```
#define ZERO_LENGTH  223.959     // mm. just about 224
   sqrt(MOTOR_OFFSET_Y*MOTOR_OFFSET_Y + MOTOR_OFFSET_X*MOTOR_OFFSET_Y))
        the length of the hypotenuse of the right trangle
        from motor center points to the top left/right corners
        of the machine area
```

The forward edge of the "zero stop" white lines are painted on the
belt 21.4 mm from the center of the sled.  This is 10mm "in" from the pully
when the sled is at zero cable length. The stop will get not get
triggered util the cable length is logically -10 (minus ten)
millimeters (AFTER it passes zero) while reeling in the belt
during homing.

```
#define LEFT_ZERO_OFFSET    -10.000     // mm == -500 steps
#define RIGHT_ZERO_OFFSET   -10.000
```

These allow for an approximately 7mm horizontal and vertial
"safe" zone around the machine area that the system can still
navigate in and ensures that the end stops are not triggered
within the work area.

TBD: The "max" stops are also painted in such a way as to allow a bit
more than the maximum length, but it is the zero stops that are
important in homing and all subsquent calculations and the overall
accuracy of the machine.

We cannot o use the $XY/Home/MPos existing config EEPROM space
to store these as preferences as that has a different semantic.

Modifying the above constants is possible to account for the fact
that the sensors may trigger sooner or later (not exactly on the edge)
by doing a Homing cycle and, after the "pull off" (15 mm in our case)
one could measure the distance from the white line to TDC of the pulley
and adjusting the constants until it is actually 15mm from TDC after
the pulloff.

## RC_SERVO

### Top Level Notes

The RC Servos are enabled/disabled for G0 moves and enabled for G1 moves.
So, you cannot use a "jog" command to probe zero as it will end up disabling
the servo and it will bounce fall back.  But with G1 commands, they will move
and hold their position.

The const double values in RcServoSettings.h for min/max mm's are RED_HERRINGS.
The are not used in any code.

    const double SERVO_POSITION_MIN_DEFAULT = 0.0;   // mm
    const double SERVO_POSITION_MAX_DEFAULT = 20.0;  // mm

### How they work

The basic algorithm is that an RC_Servo will send out a PWM pulse at the
correct intervals.  The PWM pulse will be between SERVO_MIN_PULSE_SEC and
SERVO_MAX_PULSE_SEC as defined in RCServoSettings.h.  Those pulses define
the 0 and maximum positions of the servo (motor).  The default settings result
in about 90 degrees on the blue SG90 servos.

These values can be "scaled" by user parameters $Z/RcServo/Cal/Max and
$Z/RcServo/Cal/Min which default to 1 to change the overall throw range.
I do not scale them at this time.

These servo positions are mapped to the'machine positions' from "Home/MPos"
to "maxTravel" which are 0 to 90 (DEFAULT_Z_MAX_TRAVEL) in our implementation,
and happen, when all is said and done, to represent degrees on the servo
(because it happens to move 90 degrees over it's range of travel).

Note that we have to set the z-bit into HOMING_DIR_MASK (global
dirInvertMask) so that the normal expected behavior takes place.

My device has the servo mounted such that it moves counterlockwise
for increasing motor positions, away from the work surface.

In my kinematics, I just pass the target position to mc_line() as the
desired position(), which is 'degrees' from some known position.

We *could* convert that accurately to mm's usng trig, but we don't.

### Feed Rate and Acceleration

The default feed rate for the ZAXIS in the WEBUI of 100mm/min is bogus,
and really led to a lot of confusion.  That comes out to 1.6 degrees
per second which is barely noticable on the servo.  I thought it was
not working.  So, first thing is to change the WebUI preference to
something that shows it working, like 1000mm (or more) per minute.

1000 is a little slow for actual work.  4000 is better.

If the motor moves 90 units (which are degrees but FluidNC thinks are mms),
and the feed rate is 1000mm/minute, which is about 60mm/second, it would
take 1.5 seconds to move 90 degrees.  If my pen needs to move, say 20 degrees
between a safe place and the work surface that would be 1/4 t 1/2 second
per feed move, and if the max_rate is 4000mm/minute, pretty quick to retract.

### Using Inkscape and gCodeTools

1. Open or Create the Desired SVG.
2. Create a new layer for gCodeTools and lock all the actual layers in the SVG.
   With the new layer selected:
3. Go to Extensions-gCodeTools-OrientationPoints and ceate a set of
   points with zSurface=1 and zDepth=0. Pressing "Apply" will cause it to
   create Text" items into the layer for the points.  These values will
   cause it to do one pass with moves to Z0 to cut.
4. Go to gCodeTools-ToolsLibrary and add a default Tool by pressing Apply.
   You can then edit the text in the "tool" with the Inkscape Text tool.
5. Edit the tool definition to change "Penetration Feed" to 1000 (zAxis feed rate)
   The default XY feed of 400 is ok.
6. Go to gCodeTools-PathToGCode.  Under Preferences, set the Z safe height
   to 6 or 20 or whatever.
7. Make sure the Preferences-Directory is set to /junk
8. If present the files "header" and "footer" will be included in the resultant
   gcode.  RECOMMEND that these exist and just have comments in them.
9. Finally, go to the "Path to Gcode" tab and press Apply.
   (the Apply button does not work in Preference or Options window)
10. This will create a sequenced gCode ile in /junk

### other notes

1. To get 180 degrees of motion you can modify Motors/RCServoSettings.h
   and change SERVO_MIN_PULSE_SEC and SERVO_MAX_PULSE_SEC from
   0.001,0.002 to  0.0005,0.0021  .. it sort of works but especially
   the cheap blue ones "jump" backwards sometimes (not liking it for pens
   so I'm reverting to 90 degrees of 'travel'

2. You can get 180 degrees at runtime (and probably in DEFAULTS) by setting
   $Z/RcServo/Cal/Max=1 +higher and $Z/RcServo/Cal/Min=1 -lower to match the
   ratio of commenteed out ms in RCServoSettings.h.  Something like

        $Z/RcServo/Cal/Min=0.5  = 0.0005/0.001  (50% of 0.001 secnods) and
   		$Z/RcServo/Cal/Max=1.05 = 0.0021/0.002  (105% of 0.002 seconds)

   But the servos are wonky at those settings.

   Note that it would be simpler to just send the desired PWM consistently
   but FluidNC feels the need to do it incrementally (with accelleration) which
   really mucks thigs up, I think, causing, probably, the jumping around.
   To save, i guess, leaving the PWM signal from going out and parking the servos.
   I'm wonked out!

## SD Card Resistor

**I always had problems with the SDCard on power on resets**

I finally added a **1K pullup resistor from MISO(19) to 3.3V**
which seemed to make it work.

**DON'T** hookup 5V to the SDCard VCC!!  It will then drive
5V out over MISO and could damage the ESP32.

**The 1K pull on MISO made it work.**

Adding the SD Card Module to my prototype circuit required almost
no code changes (except to fix a stack overflow) but was complicated
to learn and do.   So I record these notes:

The SD Card is not commented/documented very well.

The SD Card makes use of the pin defaults in the Espresif-ESP32 SD/FS libarary,
where the CS (chip select) pin is "GPIO_NUM_5" and the standard MOSI,MISO, and CLK
pins are used.  I list them here as a reminder

    #define SDCARD_CS    GPIO_NUM_5
    #define SPI_CLK      GPIO_NUM_18
    #define SPI_MISO     GPIO_NUM_19
    #define SPI_MOSI     GPIO_NUM_23

There is some kind of "SDCard detection scheme" in FluidNC
that I do not understand.   In any case, you should leave
SDCARD_DET_PIN undefined.  At one point I tried the following
and it did not help: $define SDCARD_DET_PIN GPIO_NUM_5

Any time I would try to access the file window from the WebUI,
the ESP32 would crash.  It turned out to be a stack overflow
that I "corrected" below, but I didn't understand it at first,
and so I started by trying to put debugging in SDCard.cpp's
get_sd_state() method, which is where it eventually calls SD.begin().
I could make no progress.

I compiled the ESP32 example SDCard program and it worked fine.
So I added code to prh_v_plotter.cpp machine_init() to call SD.begin()
and report the type, size, total, and used space on the SD Card during
initialization.  That worked fine and is now ifdef'd out.

Then I was able to learn that I could hit the SD Card via the
Serial (gcode) command line, but it was obscure information.
There is an obsolete webpage up that says you can use the $FM
command to mount the SDCard and $F to list files, but those give
"Error:20" (unsupported GCode).

### MISO Pullup Resistor

- Initializing the SDCard is inconsistent.
- A 50K pullup from MISO to 3V was recommended on the net.
- A 10K that I had handy seemed to help.

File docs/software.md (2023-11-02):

# The vMachine - Software

**[Home](readme.md)** --
**[History](history.md)** --
**[Hardware](hardware.md)** --
**[Electronics](electronics.md)** --
**Software** --
**[Installation](installation.md)**



The above diagram gives a birds-eye view of the architecture of the
vMachine software.

At the top, the *code in this repository* includes
the main *Arduino Sketch* **_vMachine.ino** file which
implements the usual Arduino *setup()* and *loop()* methods.

Below that the **vMain** layer/component *(cpp file)* contains the
**glue** (mostly overridden *weakly bound* methods) to **FluidNC**.
Most of the vMachine specific functionality is implemented in this
component.  It initializes and makes use of the **vKinematics** and
**vSensor** classes and knows about the **vMachine** *(configuration
settings*) so that it can implement things like the *triangular
coordinate* system transformations and the *homing* algorithm.

The **vMachine class** itself *(cpp and h files)* mostly contains
the *configuration settings* that are specific to this
*FluidNC based CNC machine*, but almost no other functionality.
The vMachine specific settings (like the machine width and height,
the distance between the motors, etc)
are visible to, and used by the components above it as needed.

There is also a small optional compnenent, the **ws2812b.h** file which
presents a thin wrapper around, and a few color constants for use
with, the **adafruitNeoPixels** library if the LEDS are inluded
in the build.

Below the *dotted line* in the digram are the other libraries and
code used by the vMachine.

In my architectural diagrams **visibility**
is connoted vertically in **layers**, and within layers there are
**components**. Typcially, but not always, *components* are synonymous
with C++ *classes*.
Things higher in the diagram *can see* (know about) the components and
layers below them, but things in lower layers cannot see (do not know about)
things above them.  Components at the same level in the diagrams have *varying
degrees* of visibility of one another, depending on the detailed design.

The vMachine makes use of my
[**FluidNC_Extensions**](https://github.com/phorton1/Arduino-libraries-FluidNC_Extensions)
library and my
[**FluidNC_UI**](https://github.com/phorton1/Arduino-libraries-FluidNC_UI)
library.  The FluidNC_UI library is in turn, dependent on the
[**TFT_eSPI**](https://github.com/phorton1/Arduino-libraries-TFT_eSPI)
library which is shown in **red**.
Within the FluidNC_extensions library there are a number
of components including the **gStatus**, **gActions**, and **gDebug**
objects and methods.

Below the seecond *dotted line* is
[**my fork**](https://github.com/phorton1/Arduino-libraries-FluidNC)
of the **FluidNC** project
repository.  The bulk of the actual functionality of the vMachine is
provided by this library.  It in turn depends on the **TMCStepper**,
**ESP32SSDP**, and **arduinoWebSockets** libraries.

And finally, at the bottom of the diagram is the **ESP32** hardware,
abstracted into a single box.

<br>

## vMachine.ino

**vMachine.ino**, as expected, contains the usual Arduino **setup()**
and **loop()** methods.

They more or less simply call the corresponding
**main_init()** and **run_once()** methods from *FluidNC*.

There is a little bit of additional code in vMachine.ino to
optionally *initialize the SD Card*.  I found that initializing
the SD Card the very first thing in the program tends to be
the best, as the SDCard does not play well with other *SPI*
devices until it has been properly initialized.

<br>

## vMain.cpp

**vMain.cpp** contains the *glue* to FluidNC which takes the form
of a number of overriden *weakly bound* methods, including:

- **display_init()** - called early from FluidNC during the call to *main_init()*
- **machine_init()** - called from FluidNC during the call to *main_init()*
- **cartesian_to_motors()** - called from FluidNC with cartesian coordinates,
converts them to triangular coordinates (belt lengths) and *"renders"* the line
by calling the FluidNC **mc_line()** method.
- **motors_to_cartesian()** - called from FluidNC when it wants to report the
*machine position* in cartesian coordinates based on the current *belt lengths*.
- **user_defined_homing()** - implements the vMachine specific *homing* method
- **user_realtime_command()** - allows for extension of the FluidNC *realtime
command* set, some of which are passed to the *FluidNC_UI* if it is included
in the build.

.. as well as the code, methods, and variables to support those methods.

<br>

## vMachine.h and cpp

Contains the **vMachine class** which is derived from FluidNC's
**MachineConfig** class.  It works within the FluidNC *YAML*
configuration scheme to provide vMachine specific configuration
settings and accessors to them for things like the machine
width and height, distance between motors, and so on, that
are used in the implementation of the kinematics, homing, etc.

The specific settings, and their default values are shown below.

- **$machine_width**            = 400 mm
- **$machine_height** 		    = 300 mm
- **$dist_between_motors**	    = 730.25 mm
- **$motor_offset_y**		    = 125.9 mm
- **$sprocket_radius**          = 4.8 mm
- **$chain_tolerance_left**     = 0
- **$right_tolerance_right**    = 0
- **$sag_correction**           = 0
- **$sled_radius**              = 0 mm
- **$guess_tolerance** 		    = 0.05 mm
- **$guess_num_max**     		= 200
- **$guess_max_chain_length**   = 1000
- **$zero_length**              = 209.849 mm
- **$zero_offset_left**         = -10.0 mm
- **$zero_offset_right**        = -10.0 mm
- **$safe_area_offset**         = 5.0 mm
- **$safe_position_z**     	    = -70 degrees
- **$line_segment_length**      = 0.5 mm

Please see **vMachine.cpp** and the implementation files for
descriptions of these settings and how they are used.

<br>

## vKinematics.h and cpp

Contains my port of the
[Maslow triangular kinematics](https://github.com/MaslowCNC/Firmware/blob/master/cnc_ctrl_v1/Kinematics.cpp).

<br>

## vSensor.h and vSensor.cpp

Contain an implemention of *infrared sensors* using
**analogRead**.  Note that this file *may* have been
obviated in the latest design revision of the sensors,
which now *may* work using **digitalRead()** directly
from within FluidNC.

<br>

## Please Also See

Please also see the other libraries and reposistories referenced on this page.

<br>
<hr>
<div style="text-align: right">
<a href='installation.md'>NEXT</a><i> - Installing and building the firmware ...</i>
</div>

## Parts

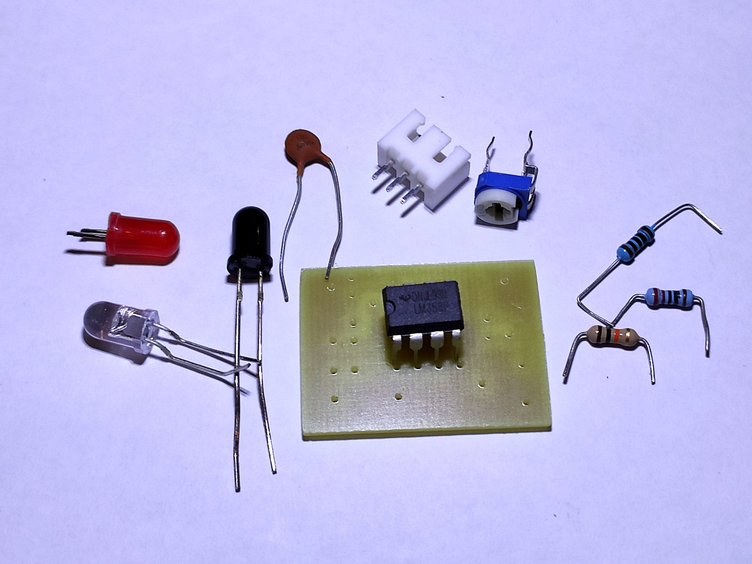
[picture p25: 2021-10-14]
docs/images/vsensor_parts.jpg

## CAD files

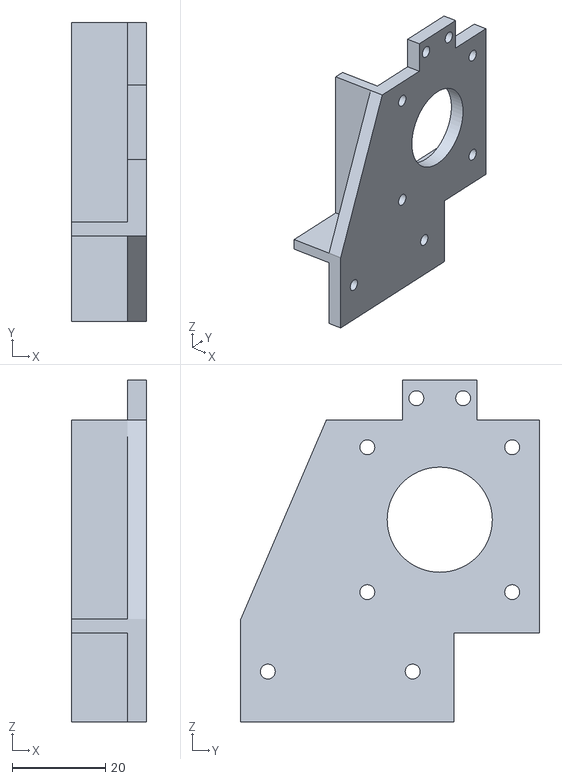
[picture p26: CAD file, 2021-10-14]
docs/stl/motor_mount_right.stl
16.0 x 63.9 x 73.2

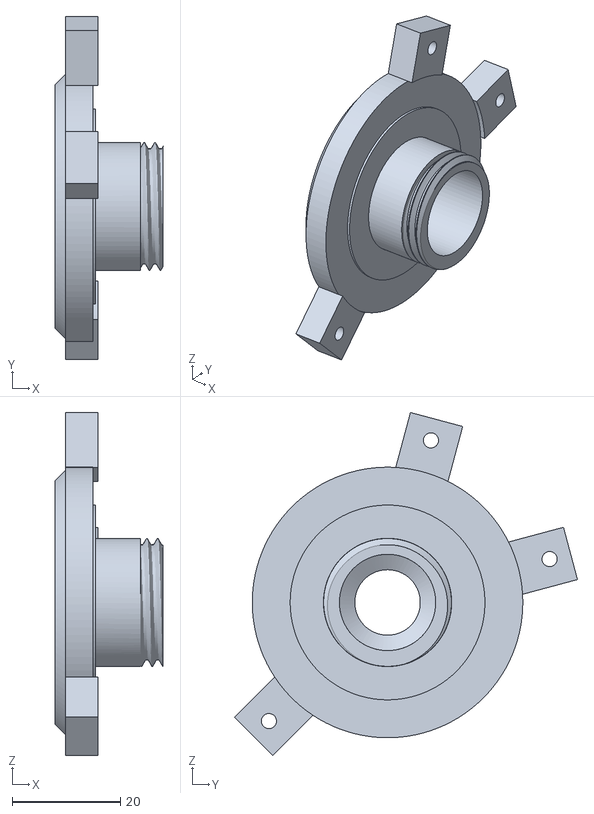
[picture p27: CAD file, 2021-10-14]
docs/stl/sled/sled_base.stl
20.0 x 63.4 x 63.4

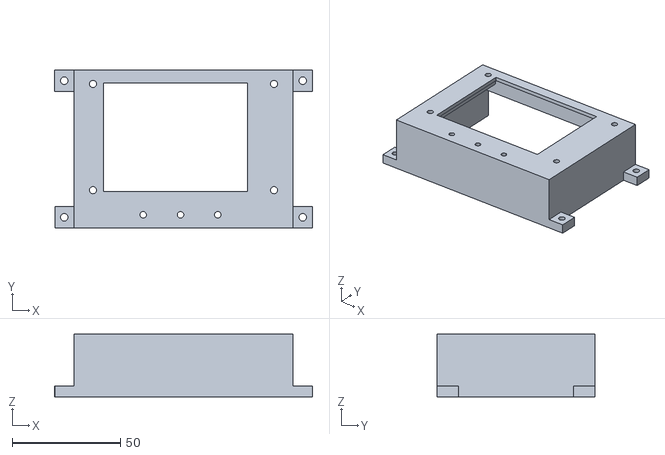
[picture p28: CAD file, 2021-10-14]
docs/stl/lcd_mount.stl
119.0 x 73.0 x 29.0

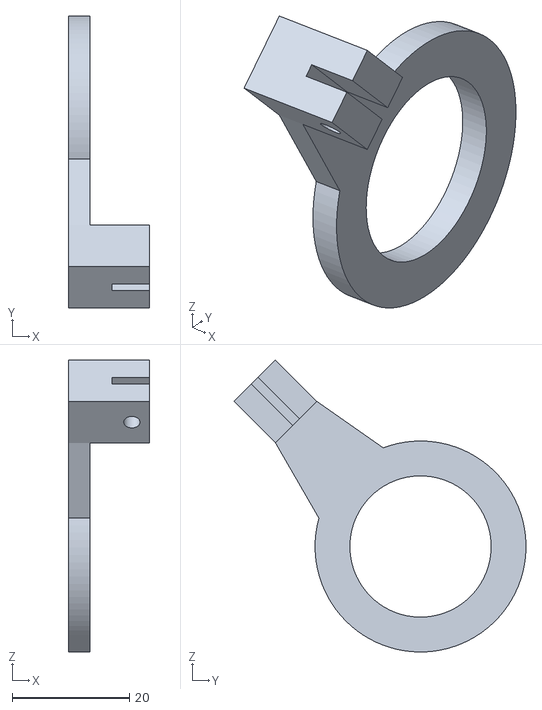
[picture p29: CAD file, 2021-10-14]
docs/stl/sled/bearing1.stl
13.8 x 49.8 x 49.8

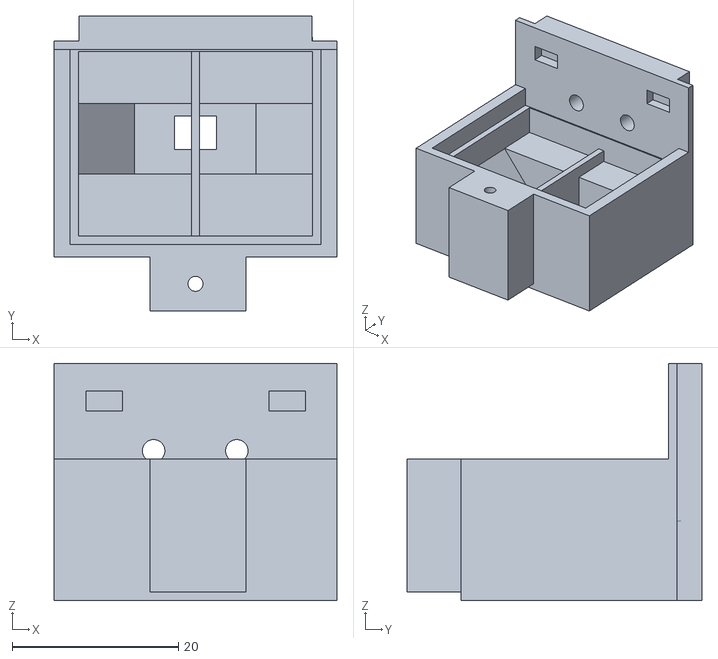
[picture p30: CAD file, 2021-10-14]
docs/stl/sensor_housing2.stl
34.0 x 35.5 x 28.5

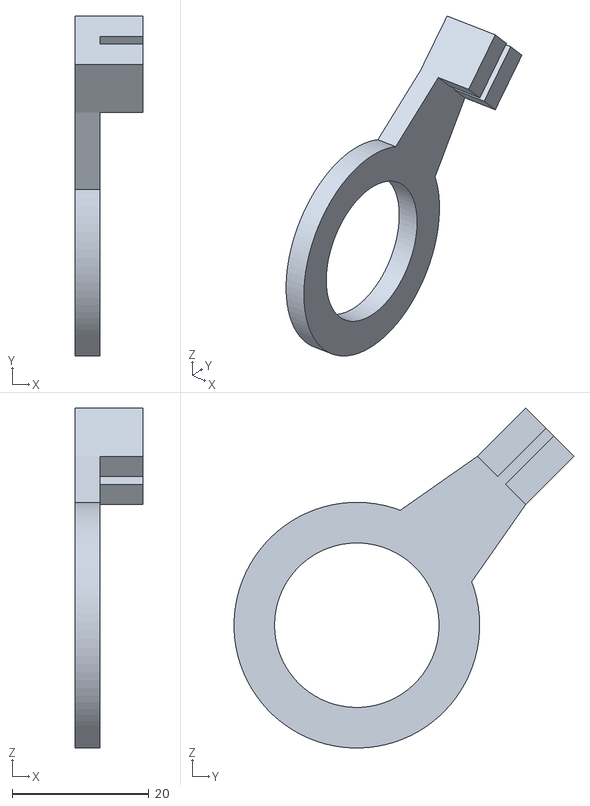
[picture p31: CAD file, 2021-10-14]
docs/stl/sled/bearing2.stl
10.0 x 49.8 x 49.8

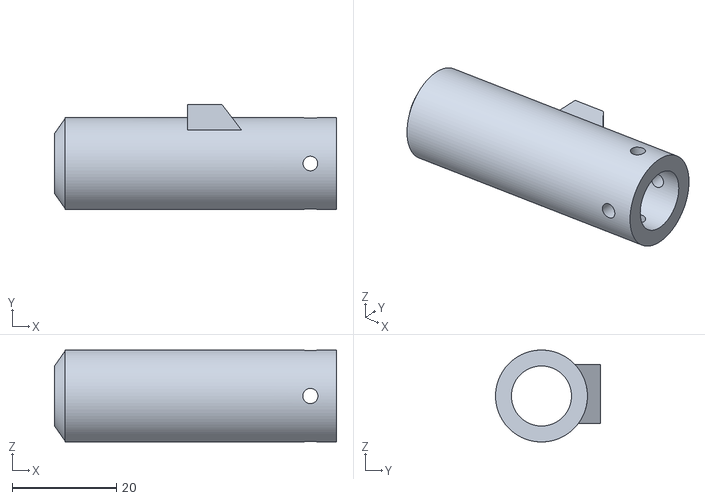
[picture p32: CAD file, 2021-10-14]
docs/stl/sled/pen_shaft.stl
54.0 x 20.1 x 17.6

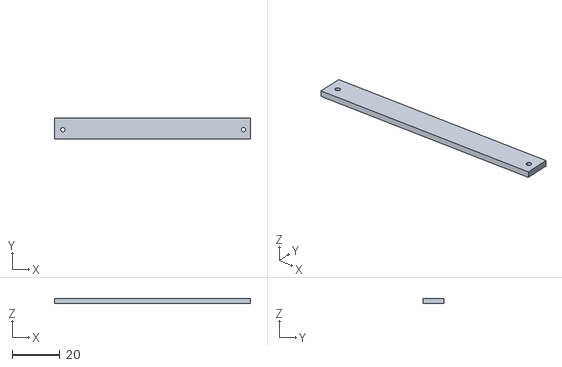
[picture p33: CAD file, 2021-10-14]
docs/stl/lcd_back_piece.stl
82.4 x 9.00 x 2.00

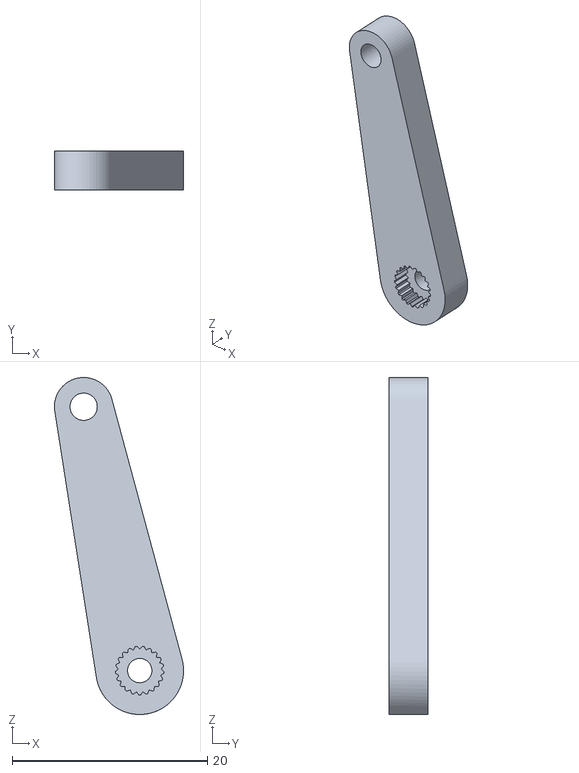
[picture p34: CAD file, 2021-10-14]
docs/stl/sled/servo_arm.stl
13.2 x 4.00 x 34.5

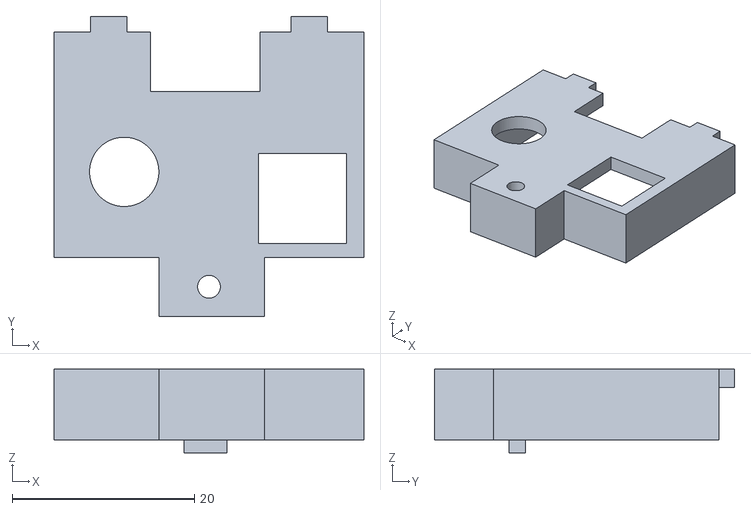
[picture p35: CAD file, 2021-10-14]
docs/stl/sensor_top2.stl
34.0 x 32.9 x 9.20

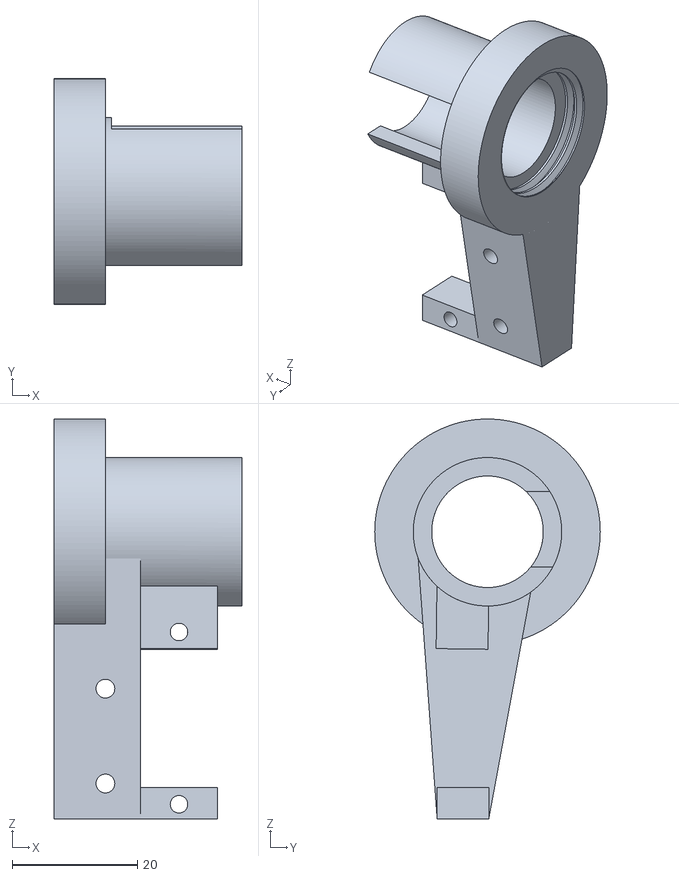
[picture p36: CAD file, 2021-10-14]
docs/stl/sled/sled_cap.stl
30.0 x 36.0 x 63.8

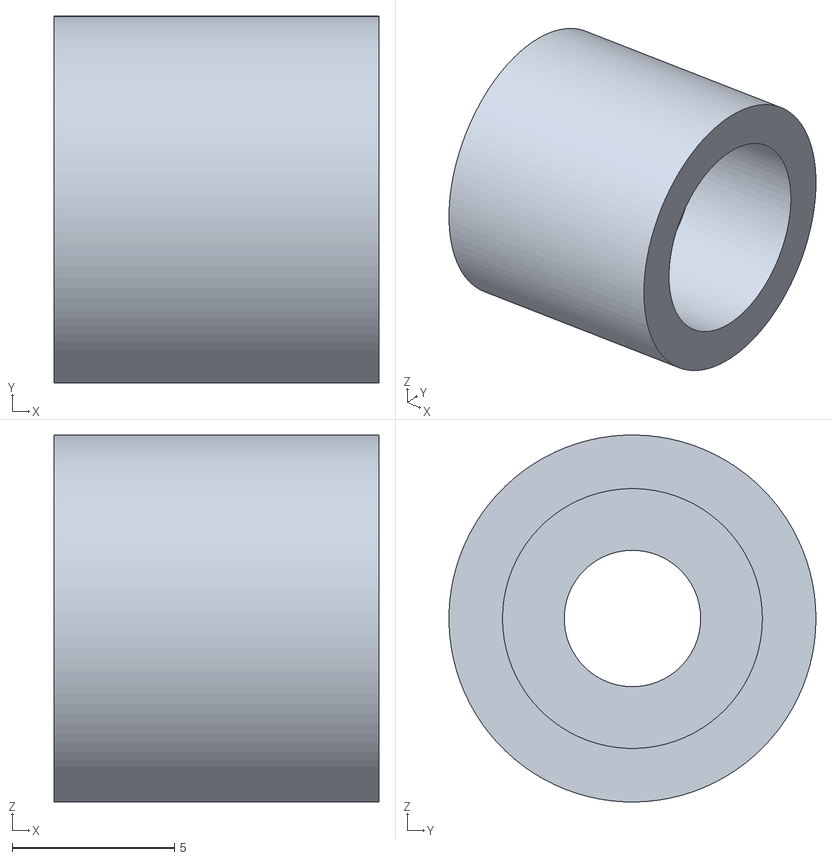
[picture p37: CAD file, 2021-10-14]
docs/stl/sled/pen_tip.stl
10.0 x 11.3 x 11.3

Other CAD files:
docs/stl/motor_mount_left.stl
docs/fusion/InfraredSensor.f3d
docs/fusion/LcdMount.f3d
docs/fusion/MotorMounts.f3d
docs/fusion/Sled.f3d

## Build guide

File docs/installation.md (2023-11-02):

# The vMachine - Installation

**[Home](readme.md)** --
**[History](history.md)** --
**[Hardware](hardware.md)** --
**[Electronics](electronics.md)** --
**[Software](software.md)** --
**Installation**

Some of these instructions are duplicated on and/or reference other pages.
Please follow the links to download and install the various pieces.

## 1. Prepare the Arduino IDE

- install the [**Arduino IDE**](https://www.arduino.cc/en/software)
- add the [**ESP32 board**](https://docs.espressif.com/projects/arduino-esp32/en/latest/installing.html)
to the Arduino IDE using the *Boards Manager*
- add the [**Arduino ESP32 filesystem uploader**](https://github.com/me-no-dev/arduino-esp32fs-plugin)
to your Arduino Sketch "tools" folder

## 2. Get the Source Code

Start by copying or cloning **this repository** into a folder called **_vMachine**
within your Arduino Sketch folder.

You then need to add a number of libraries to your **Arduino/libraries** folder.
Some of these libraries have additional dependencies on other libraries.
Please follow the instructions on the linked pages to install each library and it's dependencies.

- install my version of the [**FluidNC**](https://github.com/phorton1/Arduino-libraries-FluidNC) library and it's dependencies:
    - **arduinoWebSockets** (included in the FluidNC repository)
    - **ESP32SSDP** (included in the FluidNC repository)
    - **TMCStepper** (installed using the Arduino IDE *Library Manager*)
- install my [**FluidNC_Extensions**](https://github.com/phorton1/Arduino-libraries-FluidNC_Extensions) library
- If you are building the machine with the (optional) TFT Display
 (by default **WITH_UI** is defined in vMachine.h),
 then install my [**FluidNC_UI**](https://github.com/phorton1/Arduino-libraries-FluidNC_UI) library, and it's
 dependency:
     - [**TFT_eSPI**](https://github.com/phorton1/Arduino-libraries-TFT_eSPI) (my slightly modified and pre-configured fork of the TFT_eSPI library)
- If you are building the machine with the (optional) ws2812b LEDS
 (by default **WITH_PIXELS** is defined in vMachine.h)
 then install the **Adafruit Neopixel** library using the Arduino *Library Manager*

## 3. Build/Flash the Firmware and upload the SPIFFS

- open the **_vMachine.ino** sketch in the Arduino IDE
- select the **ESP32 Dev Module** board from the Arduino *Tools-Boards* menu
- select the **Minimal SPIFFS** (1.9MB App with OTA/190KB SPIFFS) from the *Tools-Partition Scheme* menu
- select the correct **COM Port** for the ESP32
- build and upload the firmware using the Arduino IDE **Verify/Compile/Upload** commands
- upload the contents of the vMachine *data folder* to the ESP32 *SPIFFS* using the **Tools - ESP32 Sketch Data Upload** command

<br>

## 4. Access the vMachine via the Arduino Serial Monitor

You should now be able to open the Arduino Serial Monitor (set it to **115200 baud**) and access the vMachine
via the USB serial port.  You should see something like this:

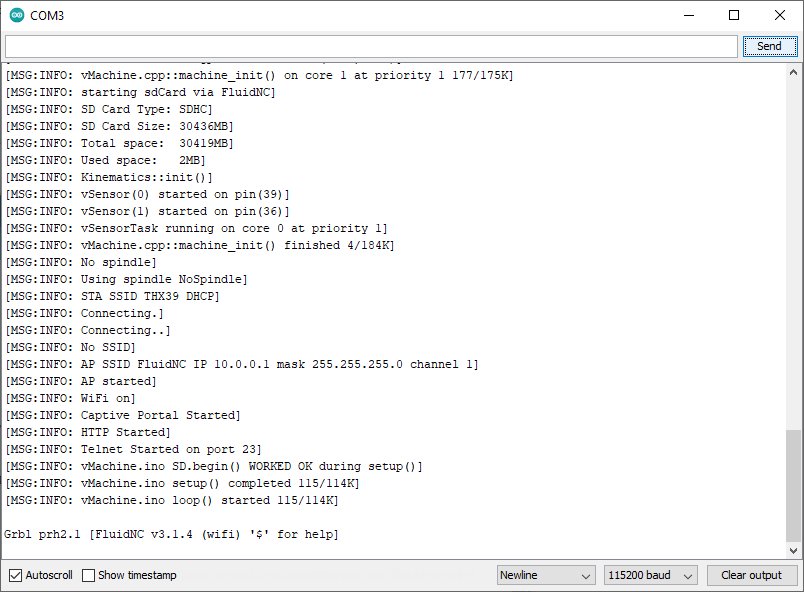
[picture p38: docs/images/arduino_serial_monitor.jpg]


You can now send GRBL (Gcode) commands to the vMachine by entering them into the
Arduino Serial Monitor and pressing the **Send** button.  Each time you press the
Send button, the vMachine should reply with **ok** in the Serial Monitor.

### Set the vMachine Coordinate Systems

From the serial monitor, send the following two commands:

```gcode
g10 L2 p2 x47.6 y35.7 z-90
g10 L2 p3 x60.3 y42.05 z-90
```

These two commands set up the **G55** and **G56** coordinate systems
to be centered pieces of **12x9** and **11.5x8** inch pieces of paper
within the vMachine's **400x300mm** work area.

These coordinate systems make it easy to draw on these specific sizes
of paper, and are **required** by the *demonstration gcode* files available in
the **sdCard** folder.

<br>

## 5. Format and prepare a FAT32 SD Card

Assuming that you are using the SDCard, please prepare one
by formatting it as necessary and copying the contents of
the **sdCard** folder onto it, and inserting it in the
SDCard module of the vMachine.

- The size of the SD Card is not very important.
- The vMachine can handle up to 32GB cards.
- Some work better than others.
- If at first it doesn't work, try turning everything off and
on, and re-inserting it the SD module.
- If you can't get it working, try a different SD card.

You can put files on the SD Card with your computer. You can also
connect to the ESP32 via Wifi and upload/delete files from the SDCard
using the **Web UI**.   You can *list* and *run* files on it from the
**Serial Port** via the *$sd/list* and *$sd/run=* commands,
or via **Touch Screen UI** *Files* window.

<br>

## 6. Connect to the vMachine with the Web UI

By default the vMachine will present itself as a Wifi Access Point called **FluidNC**

- connect your computer or phone to the **FluidNC** Wifi Access Point
- the default password is **12345678**

As soon as you connect to the FluidNC access point, a browser should pop up
and you should see the Web UI for the vMachine:

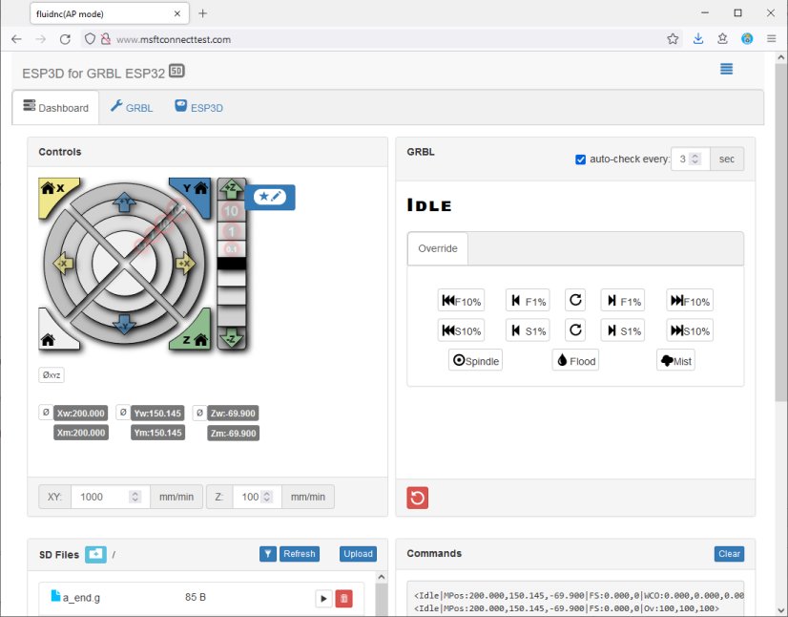
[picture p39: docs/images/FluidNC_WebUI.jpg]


If that does not happen, you ***may*** be able to access it, once connected,
via the default IP address of **10.0.0.1**.

### Configuring the Wifi

There are a number of commands that you can use to configure the
wifi for the vMachine.

You can make it connect to your
existing Wifi network by issuing the following commands:

```yaml
$Sta/SSID=YOUR_NET_SSID
$Sta/password=YOUR_NET_PASSWORD
```

You can then connect to it using the IP address given by your router,
which you can see either in the Serial Terminal Window or at the
top, in the Title Bar, of the Touch Screen UI.

It is beyond the scope of this page to describe all of the commands
and techniques that you can use to configure and modify the
vMachine.  Please see the **[Software](software.md)** page
for some details.

<br>

## 7. Finished!!

**Congratulations!  You now have burned the firmware for a working
vMachine to the ESP32 module!!!**

<br>
<hr>
<div style="text-align: right">
<a href='readme.md'>HOME</a><i> - back to the beginning!</i>
</div>

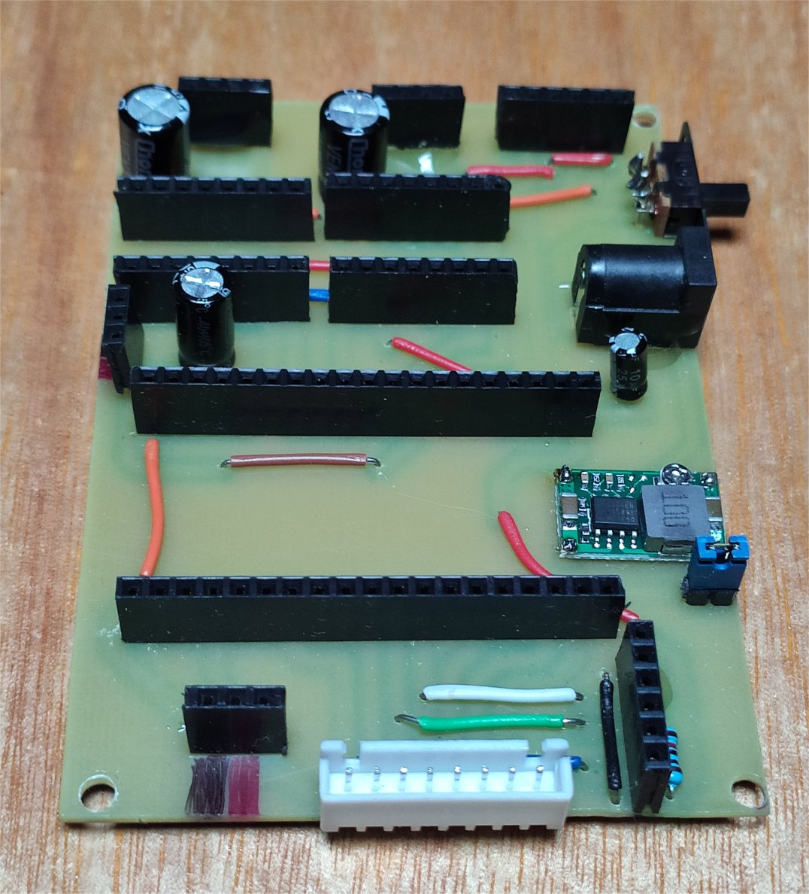
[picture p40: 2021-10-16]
docs/images/controller_soldered_large.jpg

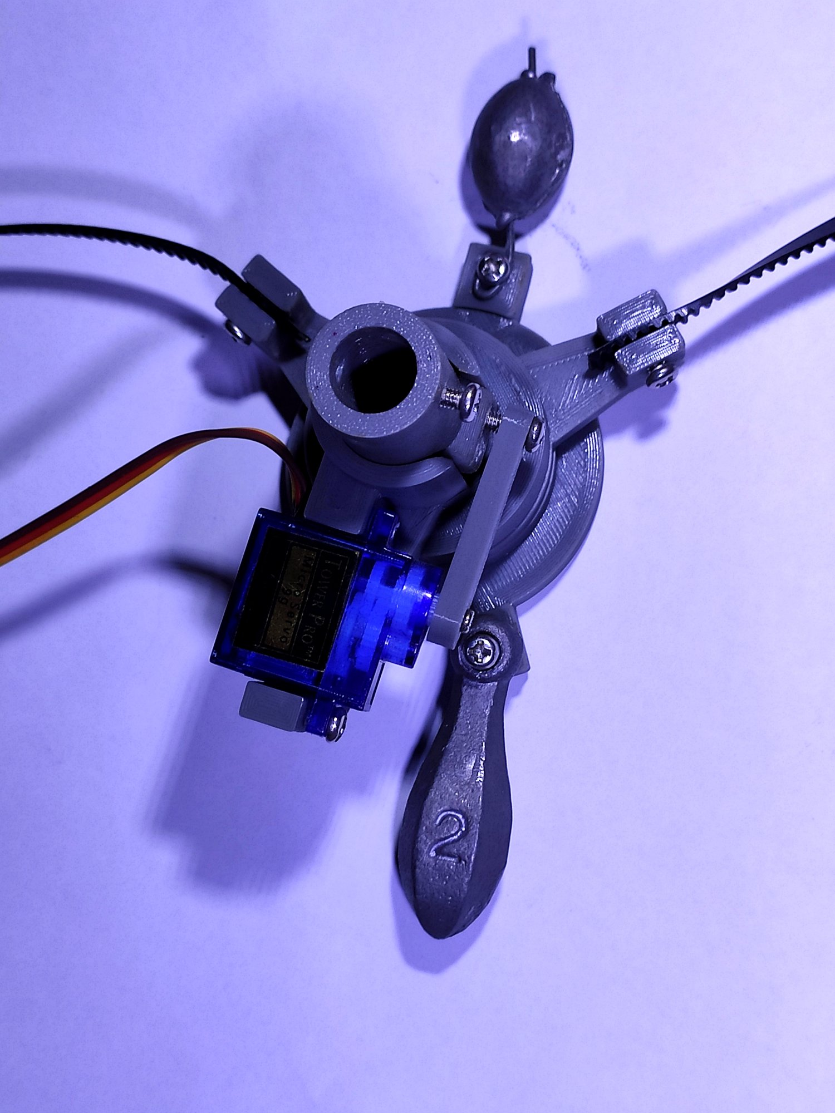
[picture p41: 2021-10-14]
docs/images/fully_assembled_sled.jpg

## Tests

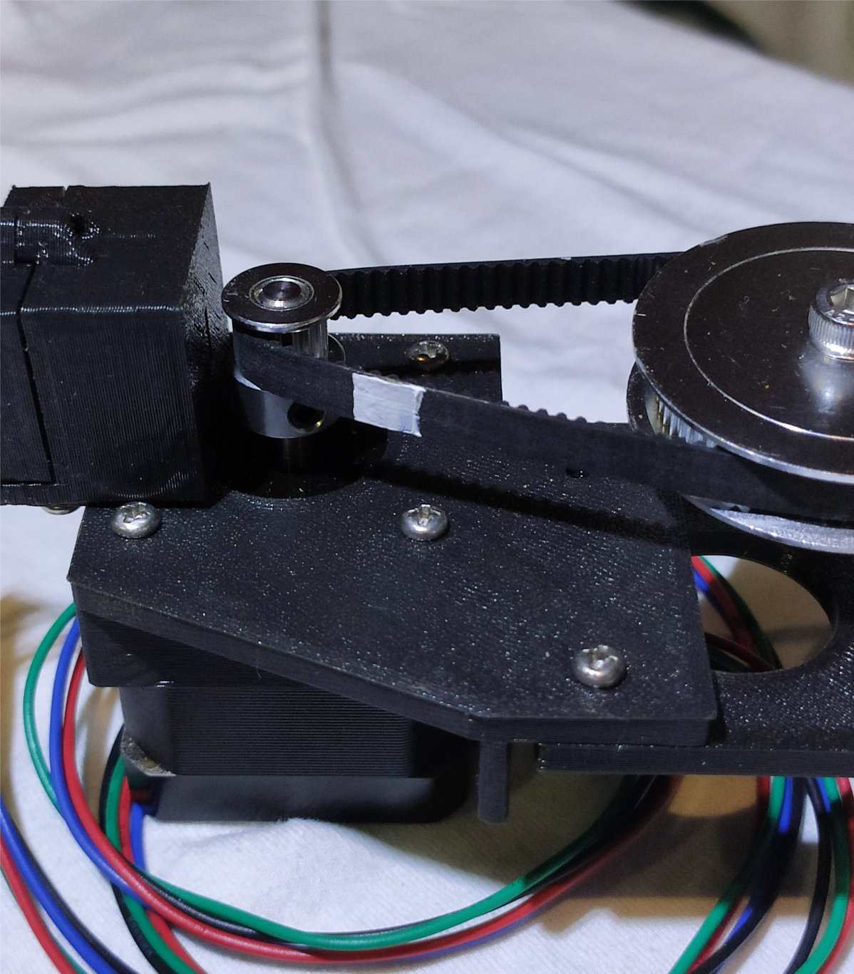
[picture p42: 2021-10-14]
docs/images/early_sensor_test.jpg

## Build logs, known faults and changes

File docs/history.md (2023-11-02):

# The vMachine - History

**[Home](readme.md)** --
**History** --
**[Hardware](hardware.md)** --
**[Electronics](electronics.md)** --
**[Software](software.md)** --
**[Installation](installation.md)**

After deciding that I would use an ESP32 for the machine, a search for available software
revealed that the best alternative for me was the **Grbl_Esp32** codebase (which has
since been advanced and renamed to **FluidNC**).   So a large chunk of work (several months)
was spent in learning **Grbl_Esp32** and porting the **Maslow** triangular kinematics software
to it.

At some point I got
it working well enough to build a machine and draw a picture.

Here is a timelapse video of the early vMachine printing a picture of a sailboat:

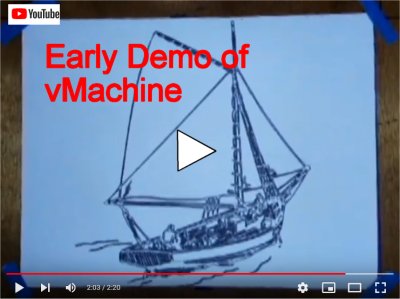
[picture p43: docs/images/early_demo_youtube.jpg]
(https://youtu.be/bSlaEzazfRE)


The version of the vMachine (that drew the above image) used a bread-boarded circuit (not soldered)
and looked like this:

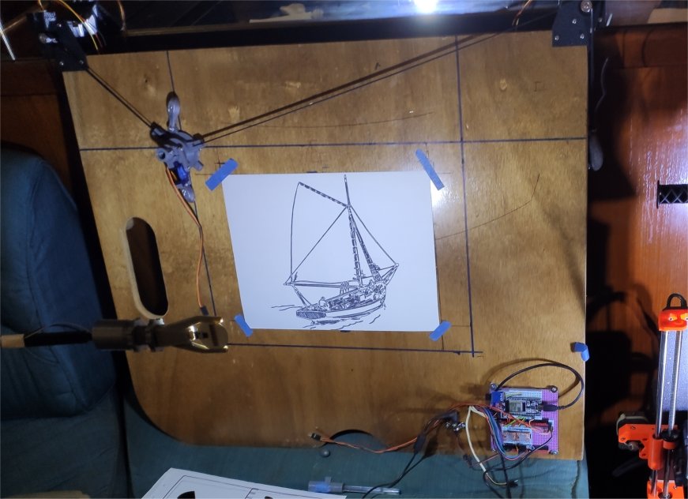
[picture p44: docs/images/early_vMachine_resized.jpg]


I like to use these [5E Board](https://www.5eboard.com/product/5eboard-high-qaulity-reconfigurable-solderless-breadboard-4x4-advanced-kit-violet-blue/)
breadboards, but you can create the basic circuit on a regular breadboard too.   The basic circuit is pretty
simple, just an **ESP32** dev board and two **A498** stepper motor drivers (with a single shared
**100uf capacitor** on the high voltage bus).   Each driver gets one pin (**green**)
from the ESP to the *STEP* input of the a498 and another pin (**yellow**) to the *DIRECTION* input.
The **blue** wire is connected from a pin on the ESP to the *ENABLE* pin on both A498's.
Otherwise, the **pink** wires connect two of the a498 step resolution selection pins to *3.3V* to
select 1/8 micro-stepping, the **red** wire provides *VCC* (3.3V) to the a498
(running underneath the board), **black** is ground (not yet hooked up to the ESP32 in this image),
and the **orange** wire (and bus at the top) is for the 19.5V I used to power the stepper motors.

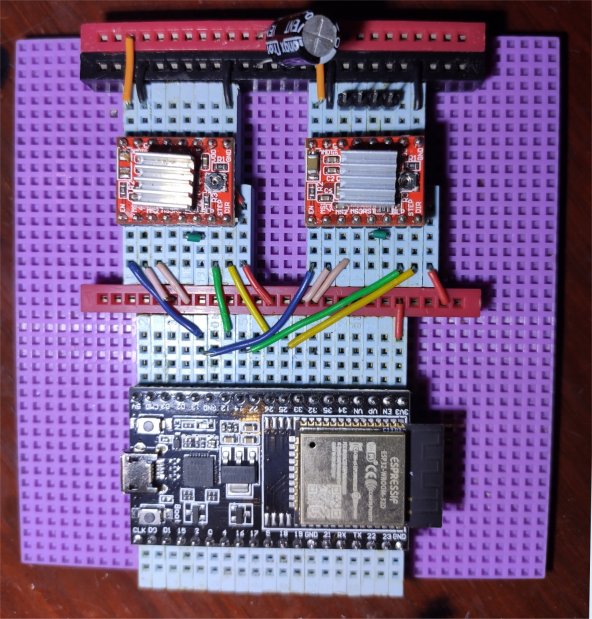
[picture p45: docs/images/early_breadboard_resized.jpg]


The stepper motors plug into the breadboard via a 4 pin header as in the upper right
of the above photo.  You can click on the image for an enlarged version.

The ESP32, as well as the code, are fairly flexible about pin assignments, and you can see
from the photo the pins I used in this early version.  The pinouts of the "final" vMachine
are a bit different and can be found on the **[Electronics](electronics.md)** page
and within the **source code** itself.

This photo is intended to merely show that the circuit is relatively simple,
and can be produced on a breadboard.  There is no SDCard or display wiring on this board,
but it could actually be used in a functional vMachine by plugging the RC Servo directly
into ground, 5V, and some other pin on the breadboard.

I used an old 19.5V 35W power supply from a broken computer i had laying around.  I removed
the jack from the broken computer and wired it up with Dupont connectors for this initial
iteration of the machine.

## Infrared Belt Sensors

An important part of this project, that took quite a bit of time coming up with, was how to
effect homing switches on the machine. In order for the triangular kinematics to
work, and in general, it is necessary that the machine **"know where it is"**.   So, before
I even built an actual machine, I decided that I would use an **infrared sensor** and a **white
stripe** painted on the belt to sense when the machine was in the *home* position.

Below is a photo of the **sensor test rig**.  I had already 3D printed the stepper motor mounts,
and tested the stepper motor's basic functionality and my ability to control them from software,
but I needed to test the sensors with a belt with a white stripe on it, so I added a pulley and
circular belt to one of the motor mounts (on the right). The pulley and belt are not part of the
actual vMachine; they were only used in this test rig. The below photo also includes housed and
mounted versions of some early infrared sensors.

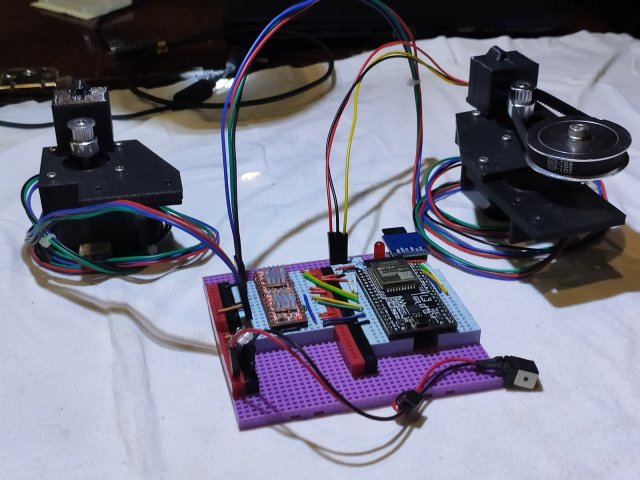
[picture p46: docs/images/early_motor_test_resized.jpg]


Once I had the pulley on, I painted a white stripe on the belt with some acrylic paint:

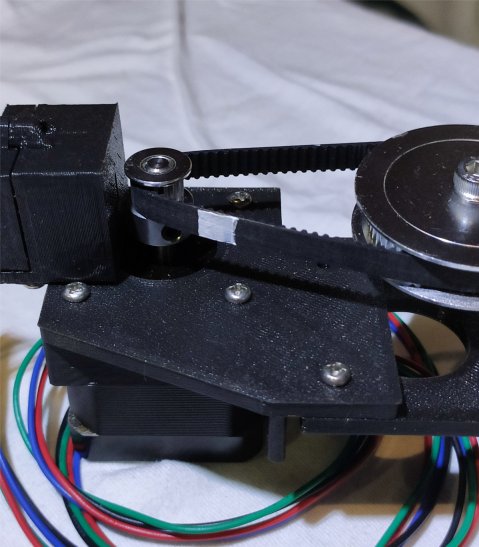
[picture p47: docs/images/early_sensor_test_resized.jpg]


And was able to test and develop the infrared sensors and 3D printed housing.

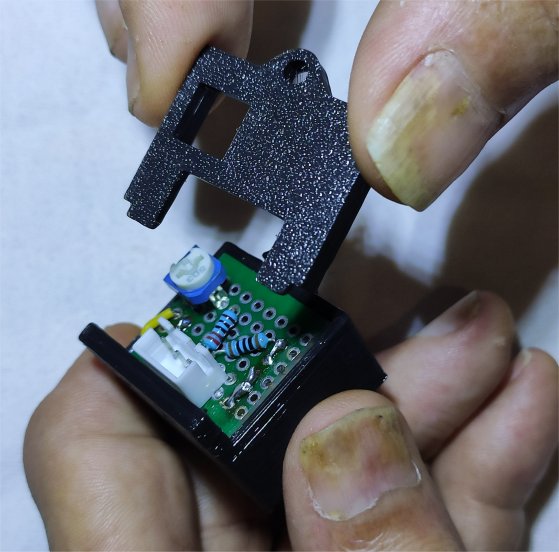
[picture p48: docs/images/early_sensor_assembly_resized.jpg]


The rudimentary infrared sensor board has been improved in the current design, but
here's a picture of the old one for posterities sake.  It emits infrared light from
one LED and measures it with the other through a small slot at the bottom of the housing,
so that it can sense when the white stripe passes over the motor pulley:

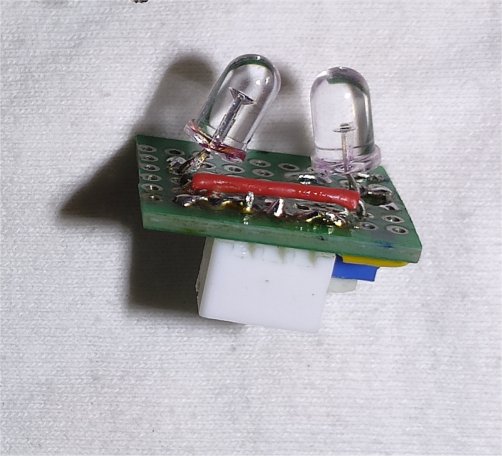
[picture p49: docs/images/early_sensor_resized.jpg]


## A Board of Some Sort

I looked around the boat for a **board** to mount the motors on, and the best board
I found was the *support for my bed*!   So I pulled the board out from under my bed, drilled
a few holes in it, and mounted the motors and breadboard on it so that I could try it:

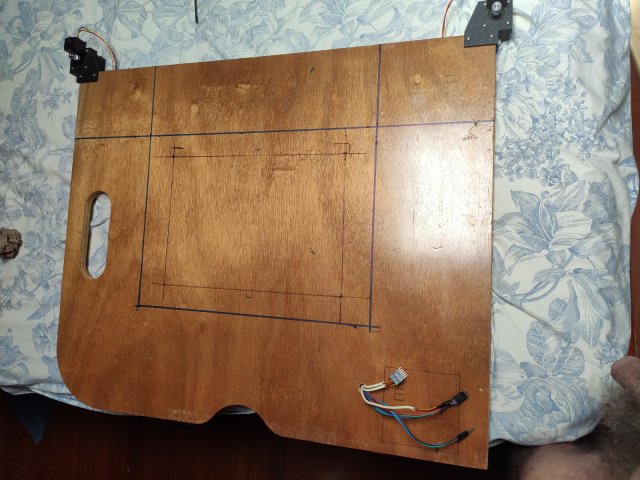
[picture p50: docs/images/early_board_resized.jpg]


## Development of Touch UI. Moving On, and Coming Back

So after a month or two of messing around with the software, electronics, and 3D printing
I finally came up with the machine above, and was able to get it basically working and
produce the timelapse video of it drawing a sailboat.

I wanted to document it at that point as a "project", but I was still very deeply involved
in the development and it felt like it was not complete.

For example, I decided I wanted to add a **touch screen user interface** which itself turned
into a fairly long-term project.  I worked on the TFT UI for at least a month or two with just
the breadboarded circuit on my desk and not installed on the "machine".

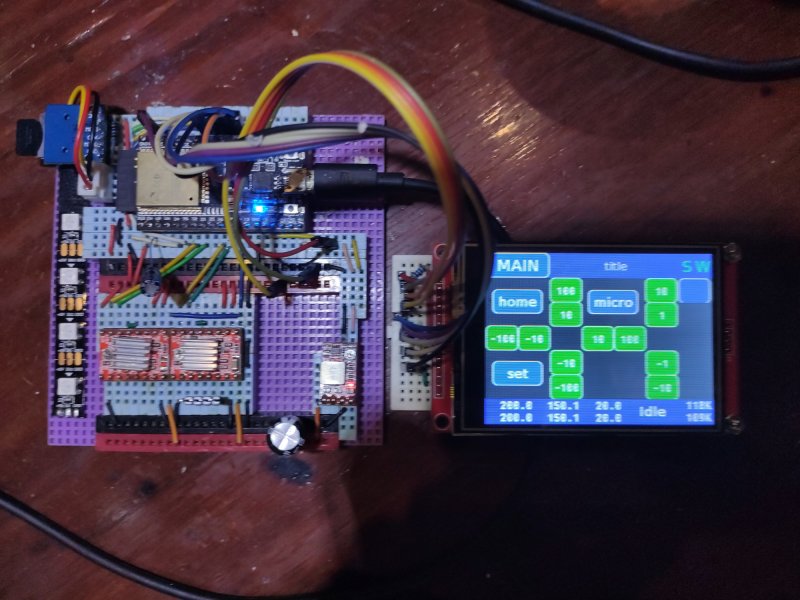
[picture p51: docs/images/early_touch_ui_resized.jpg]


I also added a **WS2812b led strip** to the circuit to allow me to display an arbitrary
number of individually addressable colored LEDs using just one pin from the ESP32.  In
the above image there is a strip of four LEDs, but in the final machine I cut it down
to three ... one for each infrared sensor that turns red when the sensor is triggered,
and one for the overall system state (blue=idle, yellow=busy, flashing red=error, etc).

The point is that one thing led to another and before I was ready to start THIS documentation
effort, I had already moved on to, and ended up completing another whole "machine" ... the
[cnc3018](https://github.com/phorton1/Arduino-esp32_cnc3018) machine.  As part of THAT process
I learned how to **mill my own PCB boards** and so, when it came time to return to
the vMachine to write this documentation, I essentially decided to rebuild it from
scratch using a home made PCB.

So I did that and these pages now describe the second, and perhaps final version of the
vMachine, and not, per-se, the machine pictured above.  Nonetheless, I wanted to preserve
some of the photos and history of my early development work on the vMachine, and so, hence,
this page.

Please continue reading to see details on how to build a physical vMachine,
install and build it's software, how to use it, and how it fits into the bigger
scheme of things ...

<br>
<hr>
<div style="text-align: right">
<a href='hardware.md'>NEXT</a><i> - the vMachine Hardware ...</i>
</div>

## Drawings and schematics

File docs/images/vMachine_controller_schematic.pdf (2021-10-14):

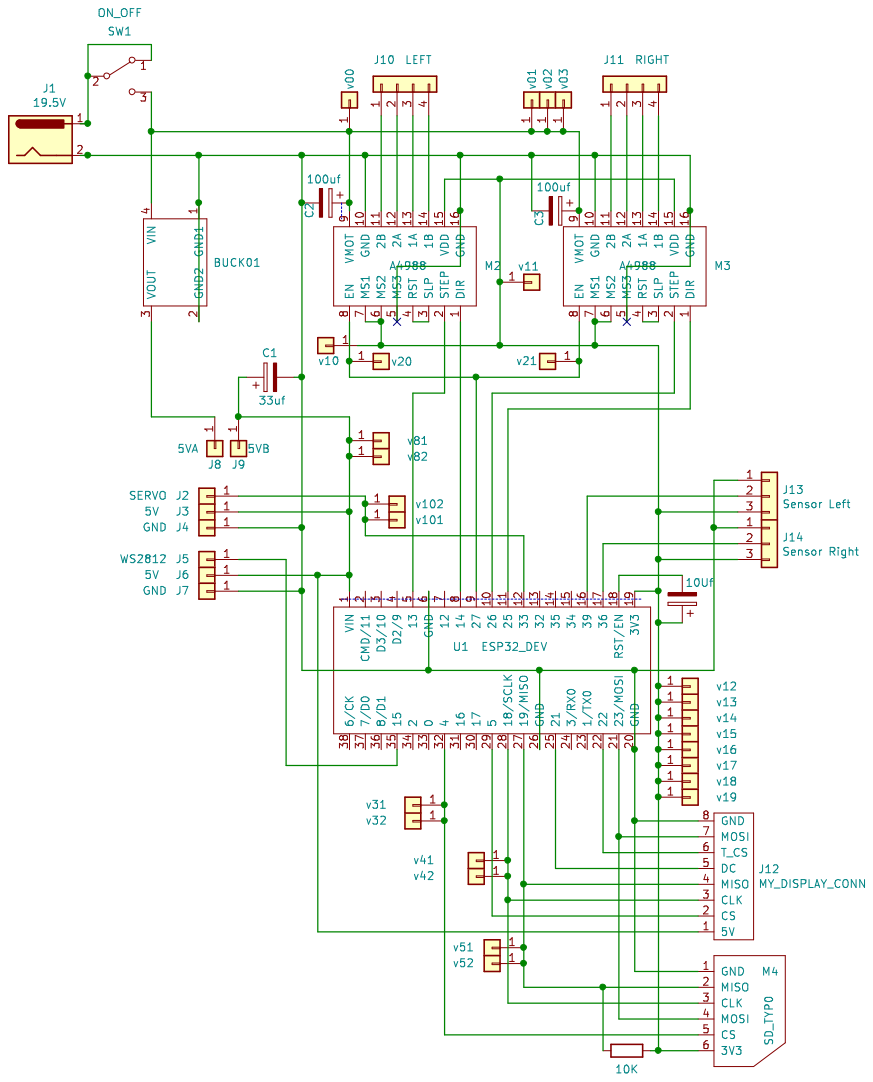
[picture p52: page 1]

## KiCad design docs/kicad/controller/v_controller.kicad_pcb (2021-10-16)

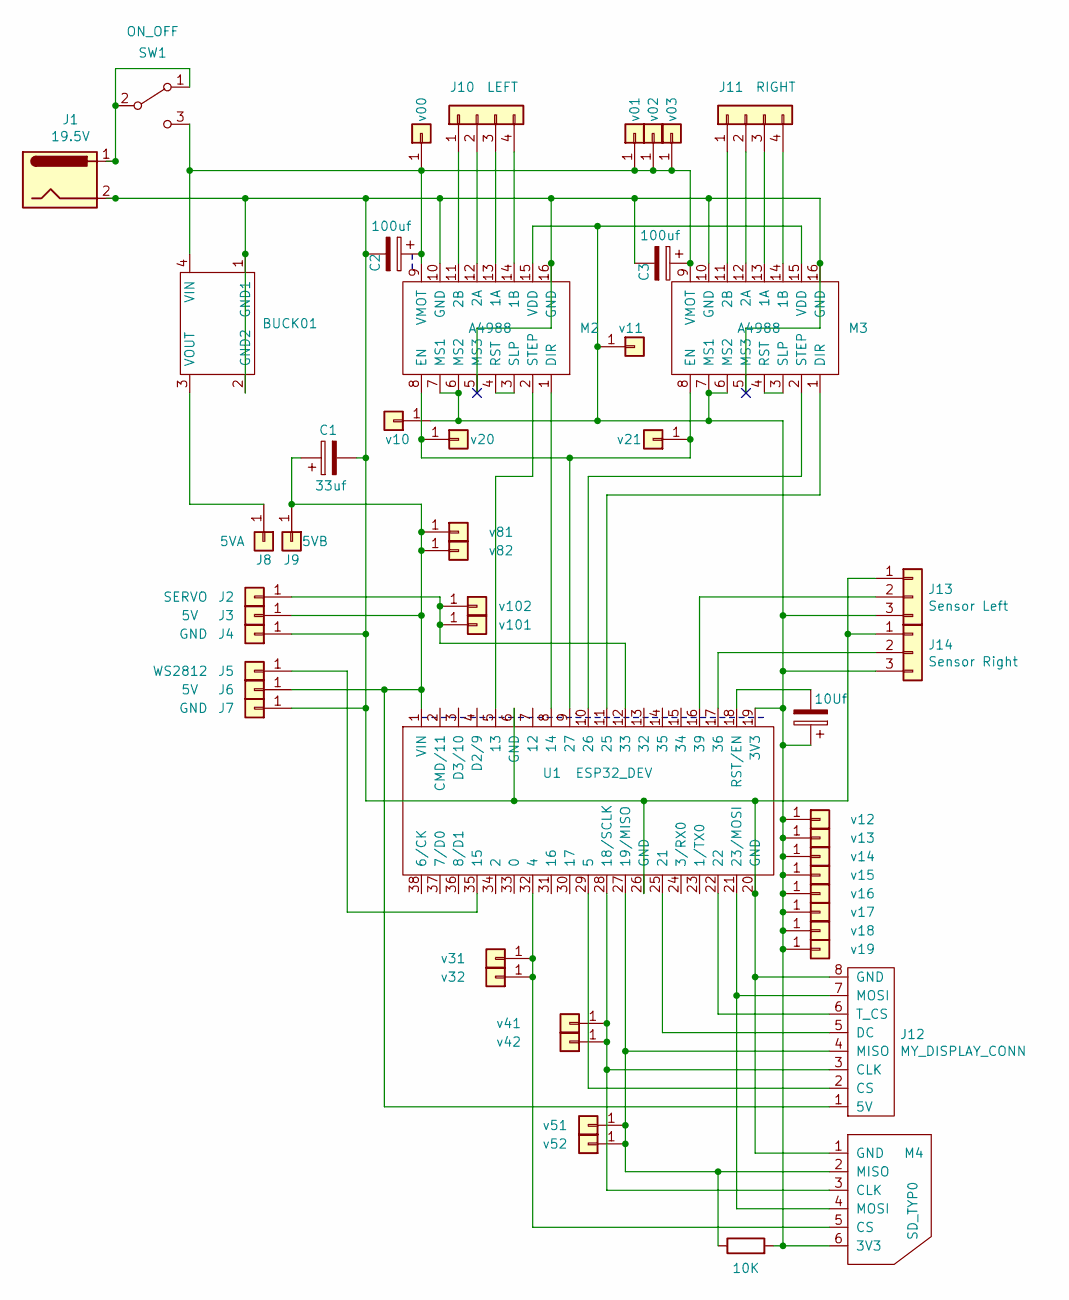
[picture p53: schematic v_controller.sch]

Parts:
C1: 33uf; my2pin
C2, C3: 100uf; my2pin
C4: 10Uf; my2pin
J1: 19.5V; myBarrelJack
J2: SERVO; my1pin
J3, J6: 5V; my1pin
J4, J7: GND; my1pin
J5: WS2812; my1pin
J8: 5VA; my1pin
J9: 5VB; my1pin
J10: LEFT; my4pin
J11: RIGHT; my4pin
J12: MY_DISPLAY_CONN; my8Pin
J13: Sensor Left; my3pin
J14: Sensor Right; my3pin
M1: BUCK01
M2, M3: A4988; a498
M4: SD_TYP0; my6Pin
R1: 10K; myResistor
SW1: ON_OFF; my3pin
U1: ESP32_DEV; ESP32-DEV
V1: v10; my1pin
V2: v00; my1pin
V3: v20; my1pin
V4: v01; my1pin
V5: v11; my1pin
V6: v12; my1pin
V7: v31; my1pin
V8: v21; my1pin
V9: v32; my1pin
V10: v41; my1pin
V11: v42; my1pin
V12: v51; my1pin
V13: v52; my1pin
V14: v13; my1pin
V15: v14; my1pin
V16: v15; my1pin
V17: v81; my1pin
V18: v82; my1pin
V19: v02; my1pin
V20: v03; my1pin
V21: v16; my1pin
V22: v17; my1pin
V23: v18; my1pin
V24: v19; my1pin
V25: v101; my1pin
V26: v102; my1pin

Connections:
unnamed: C1.1, J3.1, J6.1, J9.1, J12.1 (5V), U1.1 (VIN), V17.1, V18.1
unnamed: C1.2, C2.2, C3.2, J1.2, J4.1, J7.1, J12.8 (GND), J13.1, J14.1, M1.1 (GND1), M1.2 (GND2), M2.5 (MS3), M2.10 (GND), M2.16 (GND), M3.5 (MS3), M3.10 (GND), M3.16 (GND), M4.1 (GND), U1.6 (GND), U1.20 (GND), U1.26 (GND)
unnamed: C2.1, C3.1, M1.4 (VIN), M2.9 (VMOT), M3.9 (VMOT), SW1.3 (C), V2.1, V4.1, V19.1, V20.1
unnamed: C4.1, J13.3, J14.3, M2.6 (MS2), M2.7 (MS1), M2.15 (VDD), M3.6 (MS2), M3.7 (MS1), M3.15 (VDD), M4.6 (3V3), R1.2, U1.19 (3V3), V1.1, V5.1, V6.1, V14.1, V15.1, V16.1, V21.1, V22.1, V23.1, V24.1
unnamed: C4.2, U1.18 (RST/EN)
unnamed: J1.1, SW1.1 (A), SW1.2 (B)
unnamed: J2.1, U1.12 (33), V25.1, V26.1
unnamed: J5.1, U1.35 (15)
unnamed: J8.1, M1.3 (VOUT)
unnamed: J10.1, M2.11 (2B)
unnamed: J10.2, M2.12 (2A)
unnamed: J10.3, M2.13 (1A)
unnamed: J10.4, M2.14 (1B)
unnamed: J11.1, M3.11 (2B)
unnamed: J11.2, M3.12 (2A)
unnamed: J11.3, M3.13 (1A)
unnamed: J11.4, M3.14 (1B)
unnamed: J12.2 (CS), U1.29 (5)
unnamed: J12.3 (CLK), M4.3 (CLK), U1.28 (18/SCLK), V10.1, V11.1
unnamed: J12.4 (MISO), M4.2 (MISO), R1.1, U1.27 (19/MISO), V12.1, V13.1
unnamed: J12.5 (DC), U1.25 (21)
unnamed: J12.6 (T_CS), U1.22
unnamed: J12.7 (MOSI), M4.4 (MOSI), U1.21 (23/MOSI)
unnamed: J13.2, U1.16 (39)
unnamed: J14.2, U1.17 (36)
unnamed: M2.1 (DIR), U1.8 (14)
unnamed: M2.2 (STEP), U1.5 (13)
unnamed: M2.3 (SLP), M2.4 (RST)
unnamed: M2.8 (EN), M3.8 (EN), U1.9 (27), V3.1, V8.1
unnamed: M3.1 (DIR), U1.11 (25)
unnamed: M3.2 (STEP), U1.10 (26)
unnamed: M3.3 (SLP), M3.4 (RST)
unnamed: M4.5 (CS), U1.32 (4), V7.1, V9.1

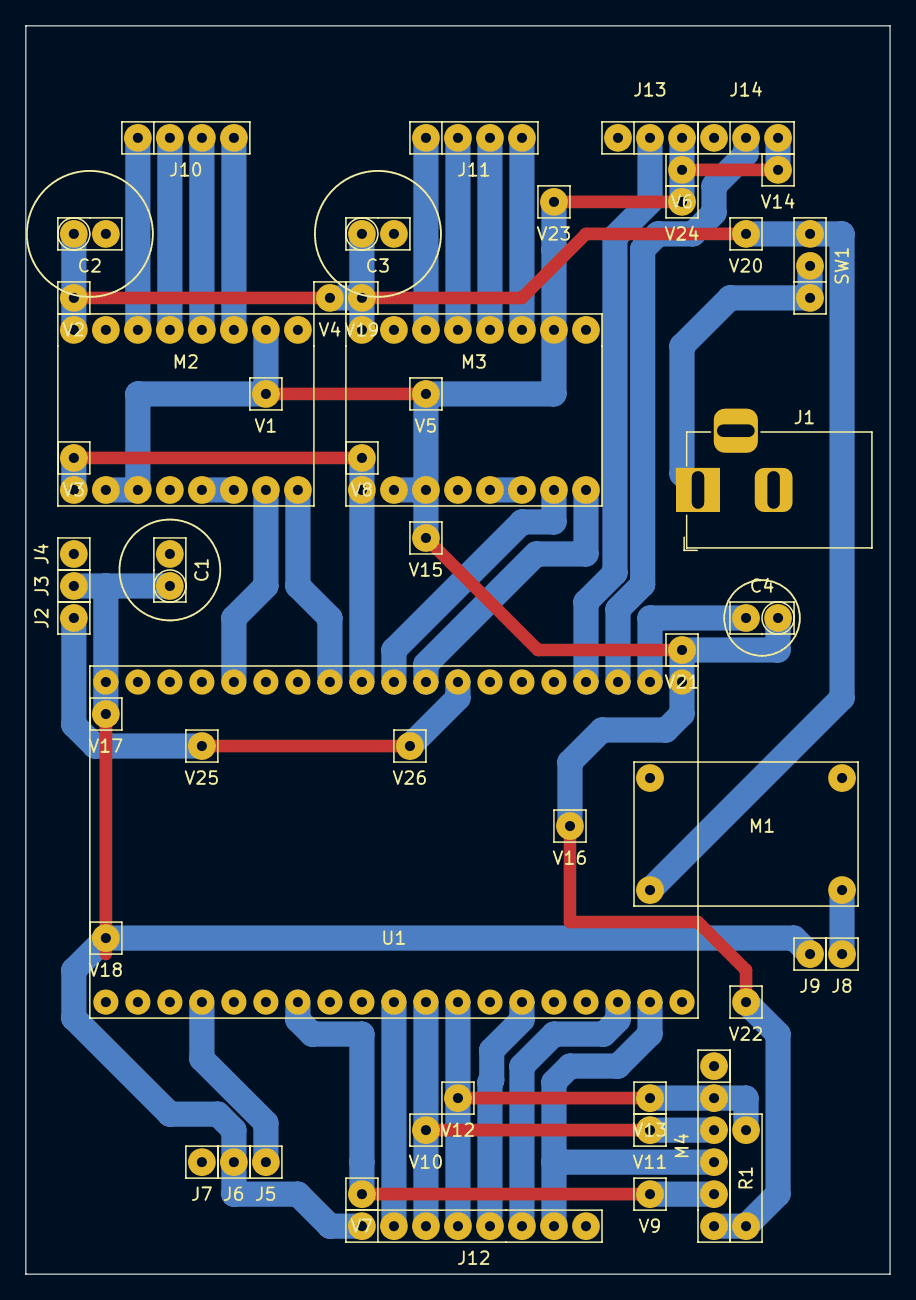
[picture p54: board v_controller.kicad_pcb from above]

Board: 2 copper layers, 68.6 x 99.1 mm, 51 parts (0 on the bottom side), 33 nets.

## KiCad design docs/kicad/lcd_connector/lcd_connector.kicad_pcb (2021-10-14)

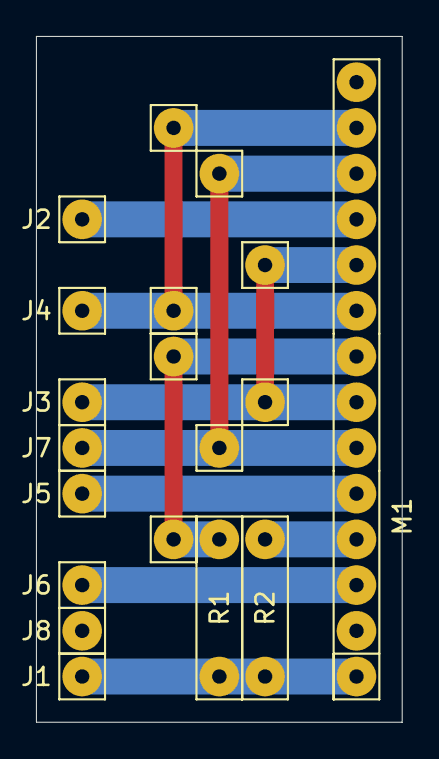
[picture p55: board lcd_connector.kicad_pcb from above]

Board: 2 copper layers, 20.3 x 38.1 mm, 19 parts (0 on the bottom side), 10 nets.

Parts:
J1: 5V; my1pin
J2: T_CS; my1pin
J3: CLK; my1pin
J4: MISO; my1pin
J5: DC; my1pin
J6: CS; my1pin
J7: MOSI; my1pin
J8: GND; my1pin
M1: TFT_ILI9341; my14Pin
R1: 100; myResistor
R2: 10K; myResistor
V1, V2, V3, V5, V6, V7, V8, V9: Conn_01x01; my1pin

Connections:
unnamed: J1.1, M1.1, R1.1, R2.1
unnamed: J2.1, M1.11
unnamed: J3.1, M1.7, M1.10, V3.1, V5.1
unnamed: J4.1, M1.9, M1.13, V6.1, V8.1
unnamed: J5.1, M1.5
unnamed: J6.1, M1.3
unnamed: J7.1, M1.6, M1.12, V7.1, V9.1
unnamed: J8.1, M1.2
unnamed: M1.4, R2.2
unnamed: M1.8, R1.2, V1.1, V2.1

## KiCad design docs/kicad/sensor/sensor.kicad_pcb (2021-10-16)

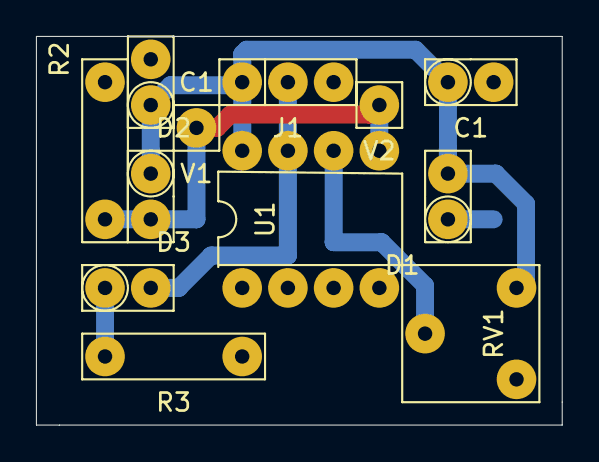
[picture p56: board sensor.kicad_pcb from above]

Board: 2 copper layers, 29.2 x 21.6 mm, 12 parts (0 on the bottom side), 6 nets.

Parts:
C1, C1#2: 100nf; my2pin
D1: IR Emit; my2pin
D2: IR_Detect; my2pin
D3: LED; my2pin
J1: Conn_01x03; my3pin
R2: 10K; myResistor
R3: 220; myResistor
RV1: 10K; myTrimPot
U1: LM393; myDip8
V1, V2: Conn_01x01; my1pin

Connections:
unnamed: C1.1, C1#2.1, D1.2, D2.1, J1.1, RV1.1, U1.8
unnamed: C1.2, C1#2.2, J1.3, R2.1, R3.1, RV1.3, U1.4
unnamed: D2.2, R2.2, U1.5, V1.1, V2.1
unnamed: D3.1, R3.2
unnamed: D3.2, J1.2, U1.7
unnamed: RV1.2, U1.6

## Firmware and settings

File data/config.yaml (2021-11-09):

# This vMachine yaml is copied to config.yaml after changes,
# so that we keep it separate from, and yet use, config.yaml.

name: "vMachine"
board: "vMachine Dev Board"

stepping:
    engine: RMT
    idle_ms: 250
    pulse_us: 2
    dir_delay_us: 1
    disable_delay_us: 0


axes:
    shared_stepper_disable_pin: gpio.27
        
    x:
        steps_per_mm: 50
        max_rate_mm_per_min: 4000
        acceleration_mm_per_sec2: 200
        max_travel_mm: 1000
        motor0:
            pulloff_mm: 15
            standard_stepper:
                step_pin: gpio.13
                direction_pin: gpio.14
        homing:
            cycle: 1
            seek_mm_per_min: 4000
            feed_mm_per_min: 400
            
    y:
        steps_per_mm: 50
        max_rate_mm_per_min: 4000
        acceleration_mm_per_sec2: 200
        max_travel_mm: 1000
        # soft_limits: true
        motor0:
            pulloff_mm: 15
            standard_stepper:
                step_pin: gpio.26
                direction_pin: gpio.25:low
                    # invert the sense of the Y directio pin
        homing:
            cycle: 1
            seek_mm_per_min: 4000
            feed_mm_per_min: 400
            
    z:
        steps_per_mm: 10
        max_rate_mm_per_min: 10000
        acceleration_mm_per_sec2: 1000
        max_travel_mm: 90
        motor0:
            rc_servo:
                output_pin: gpio.33
                # min_pulse_us: 500
                # max_pulse_us: 2200

start:
  must_home: false
    
spi:
    # one has to tell FluidNC the default ESP32 SPI pins!
    miso_pin: gpio.19
    mosi_pin: gpio.23
    sck_pin: gpio.18
    
sdcard:
    # and then one can specify the specific cs used for the SDCard
    cs_pin: gpio.4
    card_detect_pin: NO_PIN

  

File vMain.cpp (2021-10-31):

//------------------------------------------------------------------------------
// vMain.cpp
//------------------------------------------------------------------------------
// contains most of the 'glue' (overriden weakly bound methds) to FluidNC

#include <Arduino.h>
#include "vMachine.h"
#include "vKinematics.h"
#include "vSensor.h"
#include "my_ws2812b.h"
#include <FluidNC.h>
#include <Config.h>             // FluidNC
#include <System.h>             // FluidNC
#include <Logging.h>            // FluidNC
#include <Planner.h>            // FluidNC
#include <Protocol.h>           // FluidNC
#include <MotionControl.h>      // FluidNC
#include <GLimits.h>            // FluidNC
#include <FluidDebug.h>     	// FluidNC_extensions
#include <gStatus.h>			// FluidNC_extensions



#define DEBUG_VHOME   	1		// can be up to 2
#define DEBUG_VREVERSE  0
#define DEBUG_VFORWARD  0		// can be up to 2
	// debugging the inverse kinematics may introduce
	// timing problems that can crash the machine ..

#define INIT_SDCARD_AT_STARTUP   1


#if INIT_SDCARD_AT_STARTUP
	#include <SD.h>
#endif

#define STEPS_PER_MM(axis)		(config->_axes->_axis[axis]->_stepsPerMm)



//-----------------------------
// global object declarations
//-----------------------------

vMachine v_machine;
Kinematics	kinematics;
bool in_homing = false;
#ifdef WITH_PIXELS
	Adafruit_NeoPixel pixels(NUM_PIXELS,NEO_PIXEL_PIN);
#endif



//------------------------------------------------------------
// display_init() and user_realtime_command()
//------------------------------------------------------------
// Overrides of WEAK_LINK methods from FluidNC

#ifdef WITH_UI
    #include <FluidNC_UI.h>
    #include <gApp.h>

    void display_init()
        // override weak definition in FluidNC
        // called after the Serial port Client has been created
    {
        g_debug("vMachine.ino display_init() started");
        FluidNC_UI_init();
        g_debug("vMachine.ino display_init() finished");
    }


    #ifdef WITH_SCREEN_GRAB
        void user_realtime_command(uint8_t command, Print &client)
        {
            // ctrl keys
            //
            // ctrl-Q			CMD_LIVE_Z_PLUS_COARSE
            // ctrl-W       	CMD_LIVE_Z_PLUS_FINE
            // ctrl-E       	CMD_LIVE_Z_RESET
            // ctrl-R       	CMD_LIVE_Z_MINUS_FINE
            // ctrl-T       	CMD_LIVE_Z_MINUS_COARSE
            //
            // 0x01 - ctrl-A
            // 0x02 - ctrl-B
            // 0x03 - ctrl-C	concole exit
            // 0x04 - ctrl-D	console clear
            // 0x05 - ctrl-E	CMD_LIVE_Z_RESET
            // 0x06 - ctrl-F	console experimental gcode
            // 0x07 - ctrl-G	console gcode
            // 0x08 - ctrl-H
            // 0x09 - ctrl-I
            // 0x0a - ctrl-J
            // 0x0b - ctrl-K
            // 0x0c - ctrl-L
            // 0x0d - ctrl-M
            // 0x0e - ctrl-N
            // 0x0f - ctrl-O    CMD_UI_SCREEN_GRAB_PENDING
            // 0x10 - ctrl-P    CMD_UI_SCREEN_GRAB
            // 0x11 - ctrl-Q	CMD_LIVE_Z_PLUS_COARSE
            // 0x12 - ctrl-R    CMD_LIVE_Z_MINUS_COARSE
            // 0x13 - ctrl-S
            // 0x14 - ctrl-T	CMD_LIVE_Z_MINUS_COARSE
            // 0x15 - ctrl-U
            // 0x16 - ctrl-V
            // 0x17 - ctrl-W	CMD_LIVE_Z_PLUS_FINE
            // 0x18 - ctrl-X	FluidNC reset (console upload if enabled)
            // 0x19 - ctrl-Y
            // 0x1a - ctrl-Z
            // 0x1b - ESC
            // 0x1c -
            // 0x1d -
            // 0x1e -
            // 0x1f -

            g_debug("user_realtime_command(0x%02x)",command);

            switch (command)
            {
                case CMD_UI_SCREEN_GRAB :
                    gApplication::doScreenGrab(false);
                    break;
                case CMD_UI_SCREEN_GRAB_PENDING :
                    gApplication::doScreenGrab(true);
                    break;
            }
        }
    #endif  // WITH_SCREEN_GRAB
#endif  // WITH_UI



//---------------------------------------------------------------------
// static utilities used by machine_init()
//---------------------------------------------------------------------

#if INIT_SDCARD_AT_STARTUP
	static void debug_start_sdcard()
	{
		g_debug("starting sdCard via FluidNC");
		SDState state = g_status.getSDState(true);

		if (state == SDState::NotPresent)
		{
			g_info("SD Card Not Present");
		}
		else
		{
			if (state != SDState::Idle)
				g_info("SD Card BUSY");

			uint8_t cardType = SD.cardType();
			g_info("SD Card Type: %s",
				cardType == CARD_NONE ? "NONE" :
				cardType == CARD_MMC  ? "MMC" :
				cardType == CARD_SD   ? "SDSC" :
				cardType == CARD_SDHC ? "SDHC" :
				"UNKNOWN");
			uint64_t cardSize = SD.cardSize() / (1024 * 1024);
			g_info("SD Card Size: %lluMB", cardSize);
			g_info("Total space:  %lluMB", (SD.totalBytes()+1024*1024-1) / (1024 * 1024));
			g_info("Used space:   %lluMB", (SD.usedBytes()+1024*1024-1) / (1024 * 1024));
			//	SD.end();
		}
	}
#endif	// INIT_SDCARD_AT_STARTUP


static inline unsigned long mulRound(float *vals, int axis)
	// change "motor position" (chain lengths) mm's to steps
{
	float mm = vals[axis];
	float steps_per_mm = STEPS_PER_MM(axis);
	float rslt = mm * steps_per_mm + 0.5;
	unsigned long retval = rslt;
	return retval;
}


static void setDefaultPosition()
	// set system at imaginary center position to start
	// These are just imaginary values until we are homed.
{
	memset(motor_steps,0,MAX_N_AXIS * sizeof(unsigned long));

	float position[V_NUM_AXES];
	kinematics.inverse(
		v_machine.getMachineWidth()/2,		// 200
		v_machine.getMachineHeight()/2,		// 150
		&position[X_AXIS],
		&position[Y_AXIS]);
	position[Z_AXIS] = v_machine.getZAxisSafePosition(); // is 20 was 0;
	motor_steps[X_AXIS] = mulRound(position,X_AXIS);
	motor_steps[Y_AXIS] = mulRound(position,Y_AXIS);
	motor_steps[Z_AXIS] = mulRound(position,Z_AXIS);

	g_debug("init motor_steps(%d,%d,%d) mms(%f,%f,%f)",
		motor_steps[X_AXIS],
		motor_steps[Y_AXIS],
		motor_steps[Z_AXIS],
		(float)motor_steps[X_AXIS] / STEPS_PER_MM(X_AXIS),
		(float)motor_steps[Y_AXIS] / STEPS_PER_MM(Y_AXIS),
		(float)motor_steps[Z_AXIS] / STEPS_PER_MM(Z_AXIS));
}



//===========================================================
// machine_init() - override of weakly bound FluidNC method
//============================================================
// Main Entry point to the vMachine

void machine_init()
	// override weakly bound method called from FluidNC
{
	g_info("vMain.cpp::machine_init() on core %d at priority %d %d/%dK",
		xPortGetCoreID(),
		uxTaskPriorityGet(NULL),
		xPortGetFreeHeapSize()/1024,
		xPortGetMinimumEverFreeHeapSize()/1024);

	#if INIT_SDCARD_AT_STARTUP
		debug_start_sdcard();
	#endif

	#ifdef WITH_PIXELS
		pixels.begin();
	#endif

	// initialize the kinematics engine
	// and set the default position

	kinematics.init();
	setDefaultPosition();

	// start the vSensorTask

	xTaskCreatePinnedToCore(
		vSensorTask,		// method
		"vSensorTask",		// name
		4096,				// stack_size
		NULL,				// parameters
		1,  				// priority
		NULL,				// returned handle
		0);					// core 1=main FluidNC thread/task, 0=my UI and other tasks

	delay(400);		// to allow task to display it's starup message

	g_info("vMain.cpp::machine_init() finished %d/%dK",V_SDCARD_CS,xPortGetFreeHeapSize()/1024,xPortGetMinimumEverFreeHeapSize()/1024);
}



//--------------------------------------------------------------------------------------------------------
// cartesian_to_motors - override weekly bound method
//--------------------------------------------------------------------------------------------------------
// the FluidNC method params are ineptly named and ordered

bool cartesian_to_motors(float* target, plan_line_data_t* pl_data, float* position)
	// PRH THE FEED RATES NEED TO BE FIGURED OUT
	// pl_data->feed_rate = 0.5 ...
	// something about the sqrt() of the distance (per segment ?!?)
{
	float new_position[MAX_N_AXIS];
	memset(new_position,0,MAX_N_AXIS * sizeof(float));

	#if DEBUG_VREVERSE
		g_debug("cartesian_to_motors(%f,%f,%f) old(%f,%f,%f) feed=%f",
			target[X_AXIS],
			target[Y_AXIS],
			target[Z_AXIS],
			position[X_AXIS],
			position[Y_AXIS],
			position[Z_AXIS],
			pl_data->feed_rate);
	#endif
	#if DEBUG_VREVERSE>1
		g_debug("   ctm starting sys_lengths(%f,%f,%f) sys_pos(%d,%d,%d)",
			motor_steps[X_AXIS] / STEPS_PER_MM(X_AXIS),
			motor_steps[Y_AXIS] / STEPS_PER_MM(Y_AXIS),
			motor_steps[Z_AXIS] / STEPS_PER_MM(Z_AXIS),
			motor_steps[X_AXIS],
			motor_steps[Y_AXIS],
			motor_steps[Z_AXIS]);
	#endif

	#ifdef RENDER_TOOL_MOVEMENT
		extern void enqueueRenderMove(bool is_move, float *position, float *target);
		enqueueRenderMove(pl_data->motion.rapidMotion,position,target);
	#endif

	// constrain the X,Y target to the safe area

	float safe_offset = v_machine.getSafeAreaOffset();
	float machine_width = v_machine.getMachineWidth();
	float machine_height = v_machine.getMachineHeight();

	target[X_AXIS] =
		(target[X_AXIS] < -safe_offset) ? -safe_offset :
		(target[X_AXIS] > machine_width+safe_offset) ? machine_width+safe_offset :
		target[X_AXIS];
	target[Y_AXIS] =
		(target[Y_AXIS] < -safe_offset) ? -safe_offset :
		(target[Y_AXIS] > machine_height+safe_offset) ? machine_height+safe_offset :
		target[Y_AXIS];

	// prepare to do segments

	uint32_t num_segs = 1;
	float xdist = target[X_AXIS] - position[X_AXIS];
	float ydist = target[Y_AXIS] - position[Y_AXIS];
	float zdist = target[Z_AXIS] - position[Z_AXIS];

	// if neither X or Y changed, or if it's a system motion we do it in one segment
	// we round up to ensure at least one segment

	if (!pl_data->motion.rapidMotion && (xdist!=0 || ydist!=0))
	{
		float dist = sqrt(xdist*xdist + ydist*ydist + zdist*zdist);
		float line_seg_len = v_machine.getLineSegmentLength();
		float f_num_segs = (dist + (line_seg_len/2))/line_seg_len;
		num_segs = f_num_segs;
		if (!num_segs) num_segs = 1;
	}

	//--------------------
	// do loop of segments
	//--------------------

	float xinc = xdist/num_segs;
	float yinc = ydist/num_segs;
	float zinc = zdist/num_segs;

	#if DEBUG_VREVERSE
		g_debug("   ctm doing %d segments with incs(%f,%f,%f)",
			num_segs,
			xinc,
			yinc,
			zinc);
	#endif

	for (uint32_t seg_num=0; seg_num<num_segs; seg_num++)
	{
		position[X_AXIS] += xinc;
		position[Y_AXIS] += yinc;
		position[Z_AXIS] += zinc;

		kinematics.inverse(
			position[X_AXIS],
			position[Y_AXIS],
			&new_position[X_AXIS],
			&new_position[Y_AXIS]);
		new_position[Z_AXIS] = position[Z_AXIS];

		#if DEBUG_VREVERSE>1
			g_debug("   ctm seg(%d) to(%f,%f,%f) lengths(%f,%f,%f)",
				seg_num,
				position[X_AXIS],
				position[Y_AXIS],
				position[Z_AXIS],
				new_position[X_AXIS],
				new_position[Y_AXIS],
				new_position[Z_AXIS]);
		#endif

		if (!mc_line(new_position, pl_data))
			return false;	// as per polar_coaster.cpp

	}	// for each segment


	#if DEBUG_VREVERSE>1
		g_debug("cartesian_to_motors final lengths(%f,%f,%f) steps(%d,%d,%d)",
			new_position[X_AXIS],
			new_position[Y_AXIS],
			new_position[Z_AXIS],
			mulRound(new_position,X_AXIS),
			mulRound(new_position,Y_AXIS),
			mulRound(new_position,Z_AXIS));
	#endif

	return true;
}


//--------------------------------------------------------------------------------------------------------
// motors_to_cartesian - override weekly bound method
//--------------------------------------------------------------------------------------------------------

void motors_to_cartesian(float* cartesian, float* motors, int n_axis)
{
	#if DEBUG_VFORWARD
		if (prh_debug_forward)
			g_debug("motors_to_cartesian(%f,%f,%f) old(%f,%f,%f)",
				motors[X_AXIS],
				motors[Y_AXIS],
				motors[Z_AXIS],
				cartesian[X_AXIS],
				cartesian[Y_AXIS],
				cartesian[Z_AXIS]);
	#endif

	kinematics.forward(
		motors[X_AXIS],
		motors[Y_AXIS],
		&cartesian[X_AXIS],
		&cartesian[Y_AXIS]);		// useless yGuess
	cartesian[Z_AXIS] = motors[Z_AXIS];

	#if DEBUG_VFORWARD
		if (prh_debug_forward)
			g_debug("motors_to_cartesian(%f,%f,%f) final(%f,%f,%f)",
				motors[X_AXIS],
				motors[Y_AXIS],
				motors[Z_AXIS],
				cartesian[X_AXIS],
				cartesian[Y_AXIS],
				cartesian[Z_AXIS]);
	#endif
}


//--------------------------------------------------------------------------------------------------------
// Homing
//--------------------------------------------------------------------------------------------------------


static float *my_get_mpos()
{
	static float motors[MAX_N_AXIS];
	memset(motors,0,MAX_N_AXIS * sizeof(float));
	for (int idx = 0; idx < V_NUM_AXES; idx++)
	{
		motors[idx] = (float)motor_steps[idx] / STEPS_PER_MM(idx);
	}
	return motors;
}


static void debug_position(const char *what)
{
	g_debug("      %-9s sys_pos(%d,%d,%d) sys_lengths(%f,%f,%f)",
		what,
		motor_steps[X_AXIS],
		motor_steps[Y_AXIS],
		motor_steps[Z_AXIS],
		motor_steps[X_AXIS] / STEPS_PER_MM(X_AXIS),
		motor_steps[Y_AXIS] / STEPS_PER_MM(Y_AXIS),
		motor_steps[Z_AXIS] / STEPS_PER_MM(Z_AXIS));
}


static bool vHome(int axis)
	// this is unduly complicated due to the prodiguous
	//     use of global variables, undocumented assumptions about state,
	//     and the generally horrible encapsulation of functionality in
	//     the FluidNC code.
{
	#if DEBUG_VHOME > 1
		g_debug("vHome(%s)",axis?"Y":"X");
		debug_position("start");
	#endif

	int other_axis = axis == X_AXIS ? Y_AXIS : X_AXIS;
	int bit_axis = bit(axis);
	int bit_other_axis = bit(other_axis);

	#define EXTRA_TRAVEL_RATIO  1.1

	// setup empty plan data

	plan_line_data_t  plan_data;
	plan_line_data_t* pl_data = &plan_data;
	memset(pl_data, 0, sizeof(plan_line_data_t));
	pl_data->motion                = {};
	pl_data->motion.systemMotion   = 1;
	pl_data->motion.noFeedOverride = 1;
	#ifdef USE_LINE_NUMBERS
		pl_data->line_number = HOMING_CYCLE_LINE_NUMBER;
	#endif

	// get settings into variables

	auto the_axis = config->_axes->_axis[X_AXIS]; 	// we use the X cannonically
	auto homing = the_axis->_homing;

	float fast_rate = homing->_seekRate;		// DEFAULT_HOMING_SEEK_RATE;
	float slow_rate = homing->_feedRate;		// DEFAULT_HOMING_FEED_RATE;
	float pull_off  = the_axis->_motors[0]->_pulloff;			// DEFAULT_HOMING_PULLOFF;
	float other_axis_travel = EXTRA_TRAVEL_RATIO * the_axis->_maxTravel;	// out
	float axis_travel = -other_axis_travel;								// in

	// fawk - need to clear cycle stop and set the (next) axis motor_steps to zero

	rtCycleStop = false;
	motor_steps[axis] = 0;

	// setup for intial 'seek' move
	// where we wind in the axis and wind out the other_axis
	// note that the other_axis move has been made relative with +=

	float *target = my_get_mpos();				// system_get_mpos();
	target[axis] = axis_travel;					// this axis is at "0" (absoute move)
	target[other_axis] += other_axis_travel;	// relative move
	config->_axes->unlock_motors(bit_axis | bit_other_axis);

	// start initial 'seek' move

	pl_data->feed_rate = fast_rate;   			// Set current homing rate.
	plan_buffer_line(target, pl_data);  		// Bypass mc_line(). Directly plan homing motion.
	sys.step_control = {};
	sys.step_control.executeSysMotion = true;  	// Set to execute homing motion and clear existing flags.
	Stepper::prep_buffer();                     // Prep and fill segment buffer from newly planned block.
	Stepper::wake_up();    						// Initiate motion

	// check for limit hit(s)
	//
	// there are 4 parts to a successful home ...
	//    (0) we find the 'home' limit switch at the fast rate
	//    (1) we "pull off" (at the fast rate)
	//    (2) we find the home at the slow rate
	//    (3) we pull off (at the fast rate)
	//    (4) we are done
	// For fun, we repeat 2 and 3 an extra time if NUM_STEPS==6

	#define NUM_PHASES 6 		// or 4
		// candidate for preference

	int home_phase = 0;
	int home_error = 0;

	#if DEBUG_VHOME > 1
		g_debug("   vHome phase(%d)  rate(%f)  axis_travel(%f) other_axis_travel(%f)",
			home_phase,
			pl_data->feed_rate,
			axis_travel,
			other_axis_travel);
	#endif

	while (!home_error && home_phase<NUM_PHASES)
	{
		// not sure why this is needed

		Stepper::prep_buffer();

		// move volatile state into a local

		int limit_state = getVSensorState();

		// check rtReset and rtCycleStop for outer level errors

		if (rtReset)
		{
			#if DEBUG_VHOME
				g_debug("   vHome rtReset==HomingFailReset 6");
			#endif
			rtAlarm = ExecAlarm::HomingFailReset;		// 6
			home_error = 1;
		}
		else if (rtCycleStop)
		{
			if (!(home_phase & 1))
			{
				#if DEBUG_VHOME
					g_debug("   vHome rtCycleStop==HomingFailApproach 9");
				#endif
				rtAlarm = ExecAlarm::HomingFailApproach;   // 9
				home_error = 1;
			}
			else if (limit_state & bit_axis)
			{
				#if DEBUG_VHOME
					g_debug("   vHome rtCycleStop==HomingFailPulloff 8");
				#endif
				rtAlarm = ExecAlarm::HomingFailPulloff;	// 8
				home_error = 1;
			}
		}

		if (!home_error)
		{
			// if either axis hits a stop,
			// stop the other axis and continue with the main one

			if (limit_state)
				config->_axes->lock_motors(bit_other_axis);

			// if the main axis hits a stop on 0,2 we move to next state
			// if the main axis hits a stop on 1,3, it's an error
			// if we get a cycle stop on 1,3, we move to next state
			// next phase and home_error are mutually exclusive in this block

			bool next_phase = false;
			if (limit_state & bit_axis)
			{
				if (!(home_phase & 1))	// phase 1,3 etc
				{
					next_phase = true;
				}
			}
			else if (rtCycleStop)		// 0 and 2 were caught above
			{
				next_phase = true;
			}

			// move to the next phase

			if (next_phase)
			{
				home_phase++;
				Stepper::reset();  	    	// Immediately force kill steppers and reset step segment buffer.
				delay_ms(500);  		    // Delay to allow transient dynamics to dissipate.
				other_axis_travel = 0.0;

				if (home_phase & 1)
				{
					axis_travel = pull_off;
					pl_data->feed_rate = fast_rate;

					// if we hit the limit letting the other axis out,
					// for phase1 we pull IT off too.

					if (home_phase == 1 && limit_state & bit_other_axis)
						other_axis_travel = pull_off;
				}
				else if (home_phase < NUM_PHASES)
				{
					axis_travel = -pull_off * EXTRA_TRAVEL_RATIO;
					pl_data->feed_rate = slow_rate;
				}
				else
				{
					next_phase = false;	// we're done
				}

				if (next_phase)		// if still going
				{
					#if DEBUG_VHOME > 1
						g_debug("   vHome next_phase(%d)  rate(%f)  axis_travel(%f)",
							home_phase,
							pl_data->feed_rate,
							axis_travel);
						debug_position("next");
					#endif

					// the target must be reset from the motor_steps each new phase
					//     so that other axes are already where they will be targeted
					// and the system_position for the current axis must be zeroed
					// 	   or else the moves are considered to be relative to whatever tf
					//     the system position happens to be after the previous phase
					// you have to know, and manage these global variables and methods
					//     to implement a user_defined_homing() method.

					rtCycleStop = false;
					motor_steps[axis] = 0;
					target = my_get_mpos();						// system_get_mpos();
					target[axis] = axis_travel;					// absolute move
					target[other_axis] += other_axis_travel; 	// relative move to come off of stop

					// then just 5 procedure calls, all magic, sheesh, and it works

					plan_buffer_line(target, pl_data);  		// Bypass mc_line(). Directly plan homing motion.
					sys.step_control = {};
					sys.step_control.executeSysMotion = true;  	// Set to execute homing motion and clear existing flags.
					Stepper::prep_buffer();                          	// Prep and fill segment buffer from newly planned block.
					Stepper::wake_up();

				}	// next_phase <= 3
			}	// next_phase
		}	// no exec our outer cycle errror
	}	// while !home_error && home_phase<4

	if (home_error)
	{
		config->_axes->set_homing_mode(bit(X_AXIS) | bit(Y_AXIS), false);
		// motors_set_homing_mode(cycle_mask, false);
		// tell motors homing is done

		g_error("Homing fail");

		mc_reset();
		protocol_execute_realtime();
		return false;
	}
	else
	{
		#if DEBUG_VHOME > 1
			float *dbg_mms = my_get_mpos();
			g_debug("   vHome(%s) finished",axis?"Y":"X");
			debug_position("end");
		#endif

		// so, at this point, this axis is now PULL_OFF mm from the limit mark

		return true;
	}

}	// vHome() one axis
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

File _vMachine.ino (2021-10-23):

//----------------------------------------------------
// vMachine.ino
//----------------------------------------------------
// A v-type CNC machine based on the FluidNC library.

#include "vMachine.h"       // for V_SDCARD_CS
#include <FluidDebug.h>     // FluidNC_extensions


#define INIT_SD_DURING_SETUP

#ifdef INIT_SD_DURING_SETUP
    #include <SD.h>
#endif



void setup()
{
    delay(2000);

    #ifdef INIT_SD_DURING_SETUP
        bool sd_ok = SD.begin(V_SDCARD_CS);
    #endif

    main_init();        // call FluidNC setup() method

    #ifdef INIT_SD_DURING_SETUP
        g_info("vMachine.ino SD.begin() %s during setup()",sd_ok?"WORKED OK":"FAILED");
    #endif

    g_info("vMachine.ino setup() completed %d/%dK",xPortGetFreeHeapSize()/1024,xPortGetMinimumEverFreeHeapSize()/1024);
}



void loop()
{
    g_info("vMachine.ino loop() started %d/%dK",xPortGetFreeHeapSize()/1024,xPortGetMinimumEverFreeHeapSize()/1024);
    run_once();     // call FluidNC loop() method
    delay(1000);    // for display of following message to work with FluidNC asynch debug output
    g_info("vMachine.ino loop() completed %d/%dK",xPortGetFreeHeapSize()/1024,xPortGetMinimumEverFreeHeapSize()/1024);
 }

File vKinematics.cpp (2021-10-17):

/*  Copied and modified from the Maslow Control Software.

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
    Copyright 2014-2017 Bar Smith
    2021 - Patrick Horton
*/

#include "vKinematics.h"
#include "vMachine.h"

#include <FluidDebug.h>         // FluidNC_extensions


#define DEBUG_INVERSE  0
#define DEBUG_FORWARD  0
    // DEBUG_FORWARD can be upto 3 for more detail

#if DEBUG_INVERSE
    bool suppress_inverse_debugging = 0;
        // inverse debugging is, by default, disabled from forward calls
#endif

int prh_debug_forward = 0;
    // by default forward debugging is only enabled from the serial port ? command
    // see Report.cpp for prh comments


#define CHAIN_OVER_SPROCKET    1
    // versus under (I only use OVER) sysSettings.chainOverSprocket
#define USE_SAG_CALCS          1
    // whether they're compiled in or not


//------------------------------------
// note on machine dimensions
//------------------------------------
// the center of the motor is 24.3mm above the board
// the top of the "machine area" is 4" (101.6mm) below the top of the board
//
// the most critical dimensions are the distance between motor centers,
//    and the distance to the top left and right corners of the
//    "machine area", as those points represent the "zero" of the
//    X and Y chain lengths (motor positions), respectively.
//
// Everything else is calculated from those zero points.


//---------------------------------
// only used in quad calcs
//---------------------------------

#ifdef WITH_QUAD_KINEMATICS
    #define USE_QUAD_KINEMATICS     0                  // sysSettings.kinematicsType == 1
    #define SLED_WIDTH              50    // 310.0     // sysSettings.sledWidth
    #define SLED_HEIGHT             50    // 139.0     // sysSettings.sledHeight
    #define SLED_CG                 0     // 79.0      // sysSettings.sledCG (don't understand)
    #define DELTAPHI                0.001
    #define DELTAY                  0.01
    #define KINEMATICSMAXERROR      0.001
    #define KINEMATICSMAXINVERSE    10
#endif


//======================================================================
// my Kinematics
//======================================================================


Kinematics::Kinematics()
{
}


void Kinematics::init()
{
    g_info("Kinematics::init()");

    // used in triangle calcs

    dist_between_motors = v_machine.getDistBetweenMotors();     // 730.25
    safe_offset = v_machine.getSafeAreaOffset();                // 5.0
    sprocketRadius = v_machine.getSprocketRadius();             // 4.8
    halfWidth = v_machine.getMachineWidth() / 2.0;              // 200
    halfHeight = v_machine.getMachineHeight() / 2.0;            // 150
    _xCordOfMotor = dist_between_motors/2;                      // 730.25 / 2 = 365.125
    _yCordOfMotor = halfHeight + v_machine.getMotorOffsetY();   // 150 + 151.30 = 301.30

    max_forward_guesses = v_machine.getMaxForwardGuesses();
    forward_guess_tolerance = v_machine.getForwardGuessTolerance();
    max_guess_chain_length = v_machine.getGuessMaxChainLength();

    #ifdef WITH_QUAD_KINEMATICS
        Phi = -0.2;
        Theta = atan(2*SLED_HEIGHT/SLED_WIDTH);
        Psi1 = Theta - Phi;
        Psi2 = Theta + Phi;
        h = sqrt((SLED_WIDTH/2)*(SLED_WIDTH/2) + SLED_HEIGHT * SLED_HEIGHT);
    #endif
}



void Kinematics::_constrainTarget(float* xTarget,float* yTarget)
    // constrain to -half <= p <= +half +/- SAFE_AREA_OFFSET
{
    *xTarget =
        (*xTarget < -halfWidth-safe_offset) ? -halfWidth-safe_offset :
        (*xTarget > halfWidth+safe_offset) ? halfWidth+safe_offset :
        *xTarget;
    *yTarget =
        (*yTarget < -halfHeight-safe_offset) ? -halfHeight-safe_offset :
        (*yTarget > halfHeight+safe_offset) ? halfHeight+safe_offset :
        *yTarget;
}


//----------------------------------
// inverse kinematics
//----------------------------------

void Kinematics::inverse(
        float xTarget,
        float yTarget,
        float* aChainLength,
        float* bChainLength,
        bool from_forward /*= false*/)
#ifdef WITH_QUAD_KINEMATICS
    {
        if (USE_QUAD_KINEMATICS)
        {
            _quadrilateralInverse(xTarget, yTarget, aChainLength, bChainLength, from_forward);
        }
        else
        {
            _triangularInverse(xTarget, yTarget, aChainLength, bChainLength, from_forward);
        }
    }
    void Kinematics::_triangularInverse(
            float xTarget,
            float yTarget,
            float* aChainLength,
            float* bChainLength,
            bool from_forward)
#endif

    // The inverse kinematics (relating an xy coordinate pair to the required chain lengths to hit that point)
    // function for a triangular set up where the chains meet at a point, or are arranged so that they simulate
    // meeting at a point.
    //
    // The result *should* be the chain length (from the point it departs the sprocket)
    // to the point, given that 0,0 is the bottom left corner of the WORK_AREA, which is
    // (-half_width,-half_height) relative to the center of the work_area
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

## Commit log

2021-07-05 initial commit (after about 2 months of other gone repositories)
    [center.g, draw_8.5x11_paper.g, grblFileTest_old.txt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]
2021-07-09 remove nonsense due to bad idea to override core methods in Grbl_Esp32/PinMapper.cpp
2021-07-09 bring up ENABLE_TOUCH_UI with Monitor Text from Grbl_Esp32
2021-07-10 Moved SD.begin() to vMachine.ino::aetup() and that FIXED the problematic SD.begin() problems Preparing to rework Grbl_Esp32 SDCard implementation to use protectedFS
    [_vMachine.ino, vMachine.cpp, vMachine.h]
2021-07-16 Allow vMachine to choose Grbl_MinUI library or Grbl_TouchUI library
2021-07-20 init sdCard the Grbl_Esp32 way for compatability ?!? (still inconsistent)
2021-07-22 turn off annoying chain length message ...
2021-07-24 added V21812b LED Strip
2021-07-26 decouple from Grbl_Esp32 output routines; add memory footprint #defines
2021-07-26 fixed "bug" where motors were not disabled when idle that was due to yaml settings changing names and nesting levels
    [vMachine.yaml]
2021-07-29 got rid of 3d printing files
2021-08-07 a test file that shows "long endings" with Cycles after IDLE
    [a_end.g]
2021-08-07 setDefaultPosition() on homing fail to get jog working after ^X CLEAR
    [vMachine.cpp]
2021-08-08 added SYSTEM LED
2021-08-26 use <YamlOverrides.h> from new Grbl_Extras library (untested)
2021-09-23 preliminary (untested) rebase to FluidNC
    [vMachine.yaml]
2021-09-24 rename v2812b.h to my_ws2812b.h - change "Grbl_Esp32" etc to "FluidNC" etc
    [grblFileTest_old.txt, vMachine.yaml]
2021-10-07 update to new VMACH milled PC board
    [vMachine.yaml]
2021-10-11 removed www from vMachine sdCard and ruler.g from SPIFFS
    [ruler.g]
2021-10-11 NEW VSENSORS - but no real code changes - added draw_boxes.g
    [draw_boxes.g, ruler.g]
2021-10-11 cleanup yaml and demo gcode files
    [a_end.g, draw_boxes.g, ruler.g]
2021-10-14 start using config.yaml (but keeping vMachine.yaml separate)
    [vMachine.yaml]
2021-10-14 initial commit of docs (WIP)
    [InfraredSensor.f3d, LcdMount.f3d, MotorMounts.f3d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]
2021-10-14 set machine specific SSID's in YAML
    [vMachine.yaml]
2021-10-16 update CNC3018_ESP and other denormalized kiCad stuff*
    [sensor.kicad_pcb, v_controller.kicad_pcb]
2021-10-17 update to merge my fork with _main branch
    [vMachine.yaml]
2021-10-17 finish merge with _main branch of my fork of FluidNC project
    [vMachine.yaml]
2021-10-23 renamed CNC3028_ESP to esp32_cnc3018
2021-10-28 image filename case
2021-10-31 stepper notes
2021-11-09 servoTest, esp32Camera, begin new bilgeAlarm architecture
2022-04-15 implement FluidNC_UI driver/size/rotation API - rename tft calibration data files
2023-01-12 got rid of (unused) local kicad cnc3018 library
2023-01-12 Revert "delete kicad cache files"
    This reverts commit 26811d4a772752f21859dc86b1342c1c486722f3.

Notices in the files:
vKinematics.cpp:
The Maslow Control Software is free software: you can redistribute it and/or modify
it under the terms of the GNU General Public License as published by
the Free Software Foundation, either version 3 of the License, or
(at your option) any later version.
